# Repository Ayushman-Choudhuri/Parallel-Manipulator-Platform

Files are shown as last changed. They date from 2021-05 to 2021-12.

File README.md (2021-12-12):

# Circle - A Robotic Parallel-Manipulator-Platform

## 1.  Project Description

Circle is an open source 6 DOF robotic parallel manipulator platform. This project was started with the aim of building a stabilization platform for critical payloads like cameras in both linear as well as rotational axes. Additional features will be added as the project matures.   

Project link on my website: https://www.ayushmanchoudhuri.com/circle

## 2. Software

### 2.1 Software Packages Used

#### 2.1.1 Software Development
1. STM32CubeIDE - V1.2.0
2. STM32CubeMX - V6.2.0
3. STM-STUDIO-STM32 - V3.6.0
4. Jupyter Notebook 6.0.1

#### 2.1.2 Hardware Development
1. Solidworks 2018
2. Ultimaker Cura 3.4.1
3. Eagle 9.6.2

### 2.2 Setup

#### 2.2.1 STM Environment

- The Circle_Software.ioc (Software > Circle_Software.ioc) file can be imported into the STM32CubeMX environment and then the pin settings of the STM32F103C8T6 microcontroller can be viewed and modified 
- The .cproject file (Software > .cproject) can be used to import the project into the STM32CUBE IDE Environment.
- Core (Software > Core) contains all the source (Src) and the header files (inc) needed. 
- Variable Viewer (Software>Variable Viewer) contains the .tsc and .tsp files needed to view variables using STM STUDIO

#### 2.2.2 Python - IK Analysis

- The inverse kinematics analysis of the robot can be found in the  "Inverse Kinematics Solver - Python" Folder. The file can be imported into a jupyter notebook and analysed

## 3. Hardware

### 3.1 Controller

The controller is a double sided PCB with the following components mounted on it:
  - DRV8825 Stepper Motor Driver Module
  - STM32F103C8T6 Microcontroller based development board (Blue Pill). The core is an ARM CORTEX M3
  - Mini 360 Step Down Buck Converter Power Module
  - USB to UART TTL 5V 3.3V FT232RL 
  - 3 way DIP switch (To set microstepping mode of the stepper motor drivers)
  - Input port for a MPU 9250 sensor which can be attatched to the end effector for pose feedback
 
 The controller is powered using a 12V 10A SMPS power module

### 3.2 Actuation

The Actuation of the robot links are done using six NEMA 17 4.4 Kgcm motors.

### 3.3 Robot Structure and Links

The robot has a 6 RSS structure. The CAD models can be found in the file - CAD MODELS

### 3.4 Manufacturing

- All the structural support items and end effectors can be 3D printed
- If a 3D printer cannot print the base plates of the robot, they can also be made out of Acrylic sheets (min 5mm) using laser cutting methods
- The S-S links can be made by joining two femals M6 spherical joint bearings using a M6 threaded rod. 

## 4. Future Work
- Closed loop implementation and stablization using MPU 9250 sensor feedback
- Replacement of SMPS with Lithium Polymer Battery
- ROS Implementation 
- Replacing the STM 32 microcontroller with a Raspberry Pi 4

## 5. Contributing

Pull requests are welcome. For major changes, please open an issue first to discuss what you would like to change.

## 6. License

MIT

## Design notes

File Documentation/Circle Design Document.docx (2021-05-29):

CIRCLE – ROBOTIC PARALLEL MANIPULATOR SYSTEM

Written by

Ayushman Choudhuri

Version 2.0

MARCH 2021

DOCUMENT VERSION LOG

Document Version | Date of Release | Document Author | Addition Description
1.0 | 6-01-2021 | Ayushman Choudhuri | Robot Kinematics and Electronic Circuit Diagrams
2.0 | 12-03-2021 | Ayushman Choudhuri | Robot Control System

1. INTRODUCTION
2. NOTATIONS AND SYMBOL DESCRIPTIONS
3. LIST OF FIGURES
4. ROBOT DESCRIPTION

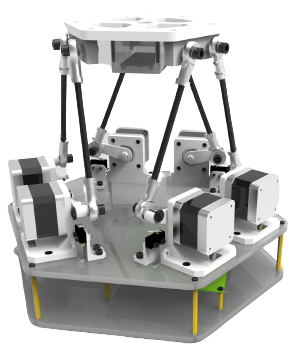
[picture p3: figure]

5. ROBOT INVERSE KINEMATICS

This section describes the inverse kinematics of the robot. Figure 1 depicts the kinematic model of the Circle robotic system. The figure shows the end effector plane, the base plane, and a linkage arm description. The end effector plane is defined by the points {E1, E2, E3, E4, E5, E6}. The base plane is defined by the {B1, B2, B3, B4, B5, B6}. The vector BOE is the translation vector between the base frame and the end-effector frame. The stepper motor arm length is described by ai, and the length of the link with an RSS configuration connecting the stepper motor arm to the end effector is si. The effective link length between the points Ei and Bi is defined by li. The base plane has a origin O at its center with X, Y, and Z as axes. The effector has an origin O’ at its center and X’, Y,’ Z’ as axes.

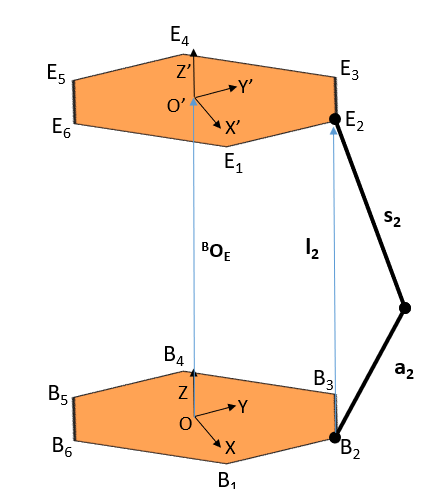
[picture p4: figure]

Figure 1: Kinematic Diagram of the Circle Robot

Each of the points {B1, B2, B3, B4, B5, B6} are the points of intersection of the stepper motor shaft axis and the motor rotation plane. Figure 2 shows the translated frame of reference (X, Y, Z) to a new motor frame of reference (X’’, Y’’, Z’’). Vector bi with its components {Δx, Δy, Δz} is the translation vector between the two frames of reference. Figure 2 shows just one instance of this translation and can be generalized to all the motors.

In the motor frame of reference, the motor plane is the plane on which the motor arm rotates. Angle β is the angle by which the plane is offset in the motor frame of reference, and angle α is the offset angle of the motor arm from the origin position for the respective motor.

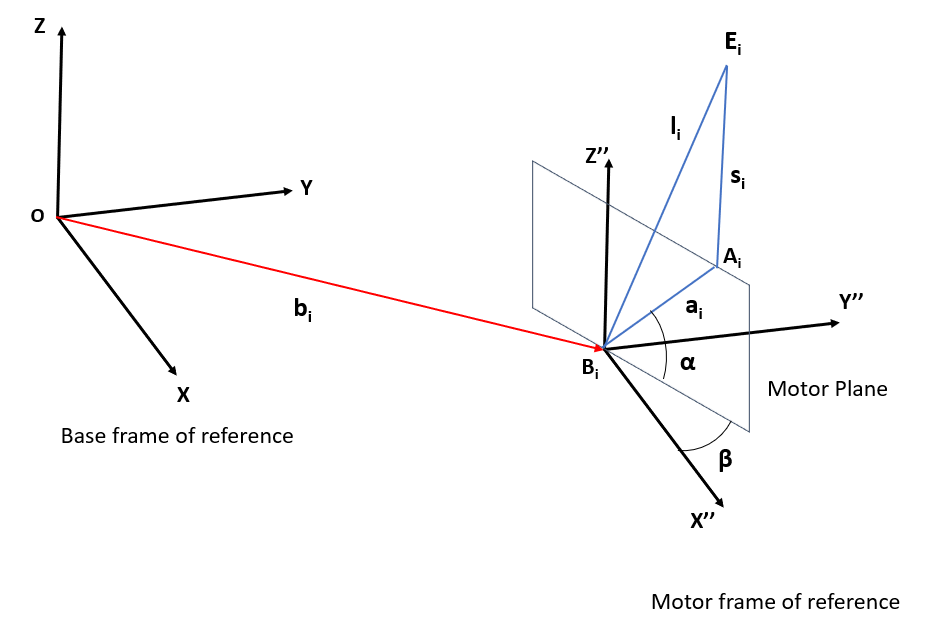
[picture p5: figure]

Figure 2: Description of the motor frame of reference with respect to the base frame origin

The points Ai, Bi and Ei have the following coordinate with respect to the base frame of reference as follows:

Ai = [ Xa, Ya, Za] T

Bi = [ Xb, Yb, Zb] T

Ei = [ Xe, Ye, Ze] T

From Figure 2, we can determine the coordinates for point Ai with respect to the base origin are:

1

Xa = ai.cosα.cosβ + Xb

2

Ya = ai.cosα.sinβ + Yb

3

Za = ai.sinα + Zb

From Pythagoras theorem, we have,

4

ai² = (Xa – Xb)² +(Ya – Yb)² + (Za – Zb)²

5

li² = (Xe – Xb)² +(Ye – Yb)² + (Ze – Zb)²

6

si² = (Xe – Xa)² +(Ye– Ya)² + (Ze – Za)²

substituting equation 4 and 5 in 6, we get

7

li² - (si² – ai²) = 2(Xb² + Yb² + Zb²) + 2Xa(Xe- Xb) + 2Ya(Ye- Yb) + 2Za(Ze – Zb) – 2(XeXb + YeYb +ZeZb)

Now substituting values of Xa, Ya, Za from equation 1,2 and 3, in equation 7 we get

li² - (si² – ai²) = 2aisinα(Ze – Zb) +2aicosα(cosβ(Xe -Xb) + sinβ(Ye - Yb ))

which is an equation of the form

L = Msinα + Ncosα

Using the trigonometric identity for sum of sine waves, we get

asinX + bcosX = csin(X+ɣ)

Where

c = sqrt (a²+b²) and tan ɣ = b/a

We thus have a sine function of α with a phase shift of δ

L = sqrt(M² + N²) sin (α + δ) where δ = tan⁻¹(N/M)

Thus

sin(α + δ) =[ L /(sqrt(M² +N²)]

Thus

αi = sin⁻¹( L/(√(M^2)+ N^2) ) – tan⁻¹( N/M)

8

Where

L = li²- (si²-ai²)

M = 2ai (Ze -Zb)

N = 2ai (cosβ(Xe -Xb) + sinβ(Ye – Yb))

Equation 8 can be used to calculate the required angles of each of the 6 motors using the link geometry parameters and the end effector coordinates as inputs.

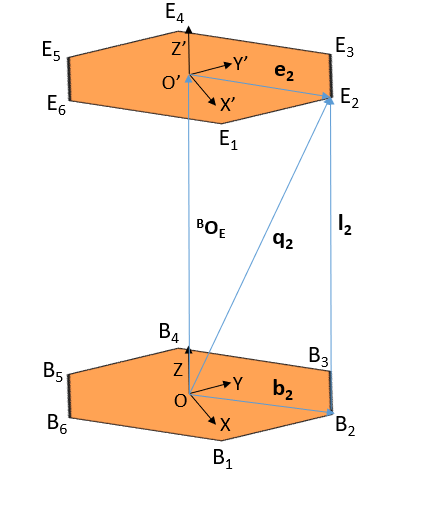
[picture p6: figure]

Figure 3: Position vectors of motor B2 and End Effector point E2 with respect to base frame, motor frame and the end effector frame of reference

From figure 3 , the position vector q2 which describes the point E2 with respect to the base frame of reference.

9

q2 = BOE + BRE.e2

Here BOE is the translation vector between the base frame of reference and the end effector frame of reference. BRE is the

rotation matrix for the end effector frame with respect to the base frame of reference.

The vector q2 can also be written as

10

q2 = b2 + l2

Hence, from equations 9 and 10 we can deduce

l2 = BOE + BRE.e2 - b2

This can be generalised to all the linkages as

11

li = BOE + BRE.ei – bi

The rotation matrix BRE for yaw ψ , pitch θ and Roll φ turns out to be:

BRE = [cosψcosθ, -sinψcosφ+cosψsinθsinφ, sinψsinφ+cosψsinθcosφsinψcosθ, cosψcosφ+sinψsinθsinφ, -cosψsinφ+sinψsinθcosφ-sinθ, cosθsinφ, cosθcosφ]

Equation 11 can be used to calculate the effective link length of any of the linkages when the yaw pitch and roll angles of the end effector frame of reference is known with respect to the base frame of reference.

6. SYSTEM ARCHITECTURE

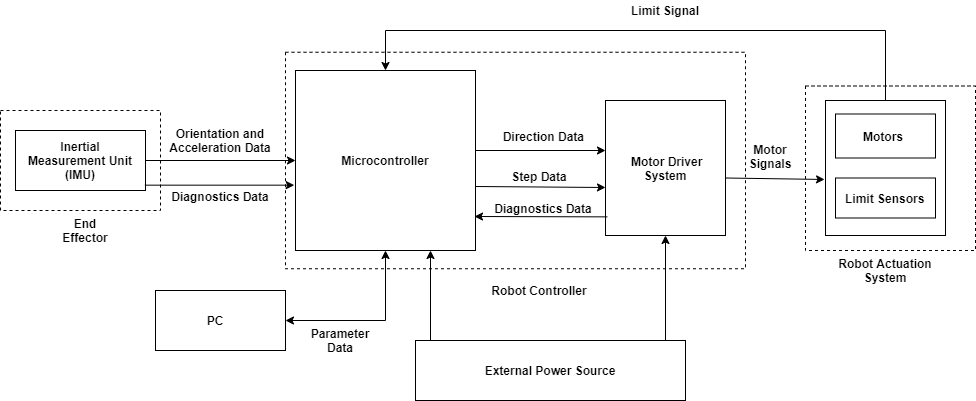
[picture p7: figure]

Figure 4: Circle System Architecture

  6.1. MICROCONTROLLER
  6.2. MOTOR DRIVER SYSTEM
  6.3. ROBOT ACTUATION SYSTEM
  6.4. INERTIAL MEASUREMENT UNIT
7. MECHANICAL DESIGN
  7.1. GENERAL DESCRIPTION
  7.2. ROBOT BASE
  7.3. ELECTRONICS BAY
  7.4. ROBOT LINKS
  7.5. END EFFECTOR DESIGN
  7.6. MANUFACTURING DETAILS
8. CONTROL SYSTEM DESIGN
9. SOFTWARE ARCHITECTURE
10. ELECTRONIC SCHEMATIC (V1)

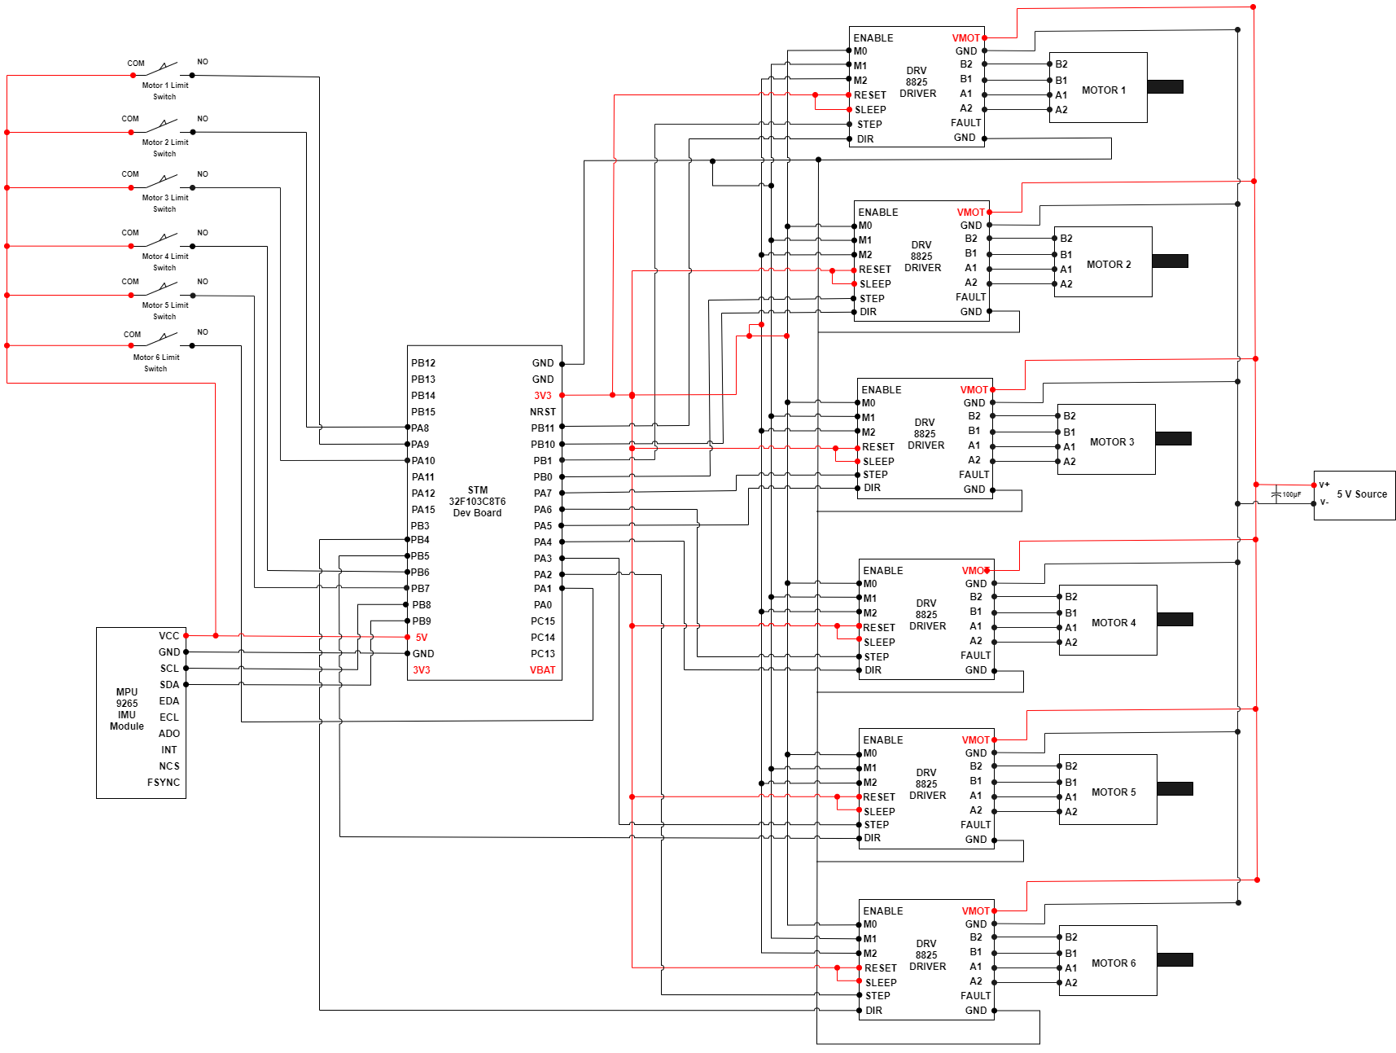
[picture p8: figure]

Figure 5: Electronic Circuit Diagram V1

11. ROBOT PARAMETERS
  11.1. END EFFECTOR PARAMETERS

Coordinates (in mm) of the end effector pivot point coordinates with respect to the end effector frame of reference.

E = [-73.7, +19.46, 0-53.7, +54.1, 0+53.7, +54.1, 0+73.7, +19.46, 0+20, -73.55, 0-20, -73.55, 0]

  11.2. BASE PARAMETERS

Coordinates (in mm) of the base pivot point coordinates with respect to the base frame of reference.

B = [-81.63, +0.36, 0-41.13, +70.51, 0+41.13, +70.51, 0+81.63, +0.36, 0+40.5, -70.87, 0-81.63, -70.87, 0]

  11.3. HOME POSITION OFFSET PARAMETERS
  11.4. INERTIAL MEASUREMENT UNIT PARAMETERS (MPU 9250)
  11.5. STEPPER MOTOR DRIVER PARAMETERS (DRV8825)
12. REFERENCES

[1] https://invensense.tdk.com/wp-content/uploads/2015/02/PS-MPU-9250A-01-v1.1.pdf

[2] https://cdn.sparkfun.com/assets/learn_tutorials/5/5/0/MPU-9250-Register-Map.pdf

[3]https://github.com/kriswiner/MPU9250/tree/master/Documents

[4]https://github.com/kriswiner/MPU9250/tree/master/STM32F401

[5]https://github.com/kriswiner/MPU9250

[6]https://www.ti.com/lit/ds/symlink/drv8825.pdf?ts=1615789139713&ref_url=https%253A%252F%252Fwww.google.com%252F

[7] https://www.pololu.com/product/2133

[8] https://www.youtube.com/watch?v=6IAkYpmA1DQ&ab_channel=HowToMechatronics

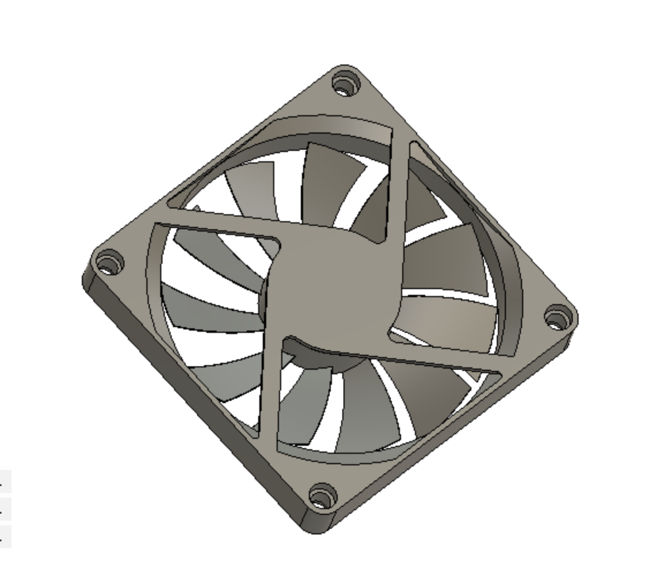
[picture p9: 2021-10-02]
CAD Models/Electronics/80 mm Fan/Screen Shot 2019-12-02 at 6.14.03 PM.png

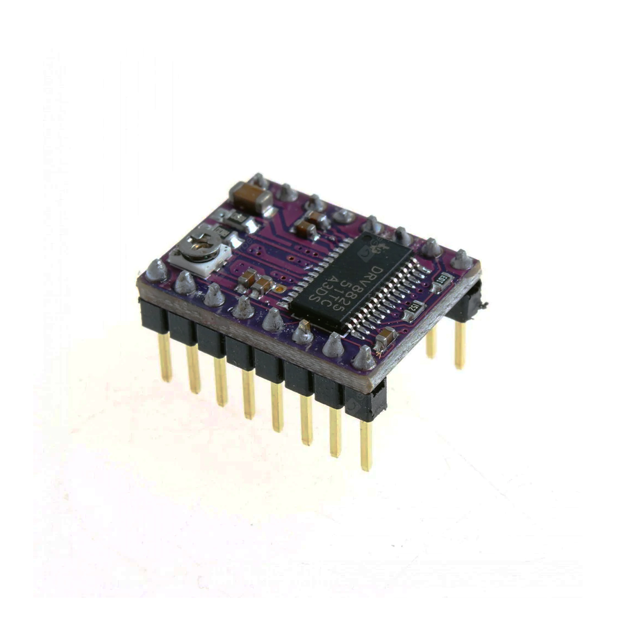
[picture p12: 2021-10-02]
CAD Models/Electronics/DRV8825/Driver DRV8825.jpg

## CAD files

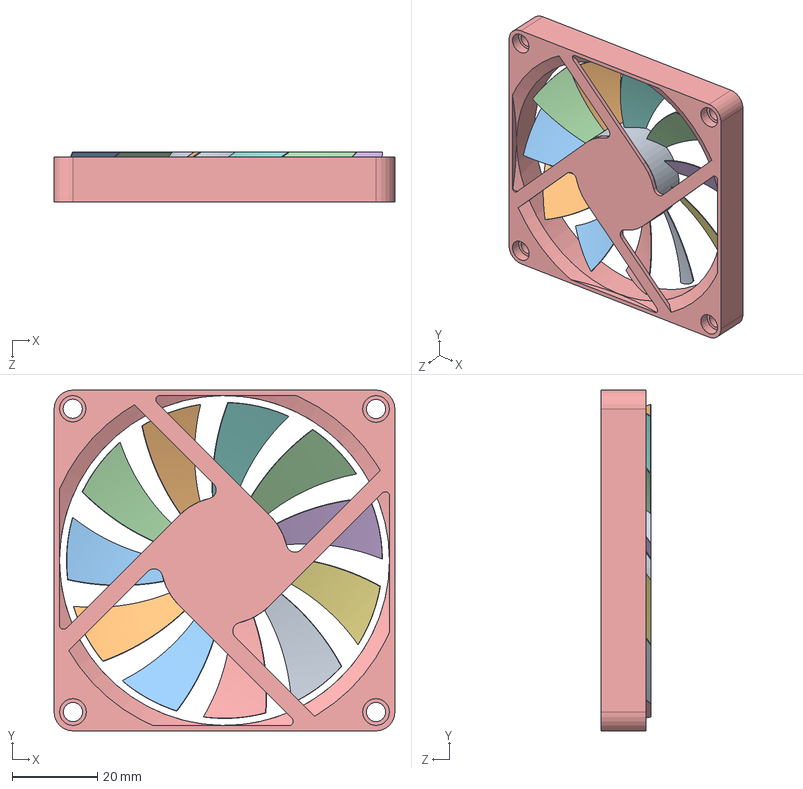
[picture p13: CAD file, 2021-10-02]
CAD Models/Electronics/80 mm Fan/GDSTIME - 5v Fan_13.sldasm
80.0 x 80.0 x 11.8 mm
GDSTIME - 5v Fan_6
GDSTIME - 5v Fan_8
GDSTIME - 5v Fan_4
GDSTIME - 5v Fan_3
GDSTIME - 5v Fan_12
GDSTIME - 5v Fan_5
GDSTIME - 5v Fan_10
GDSTIME - 5v Fan_7
GDSTIME - 5v Fan_11
GDSTIME - 5v Fan_9
GDSTIME - 5v Fan_2
GDSTIME - 5v Fan
GDSTIME - 5v Fan_1

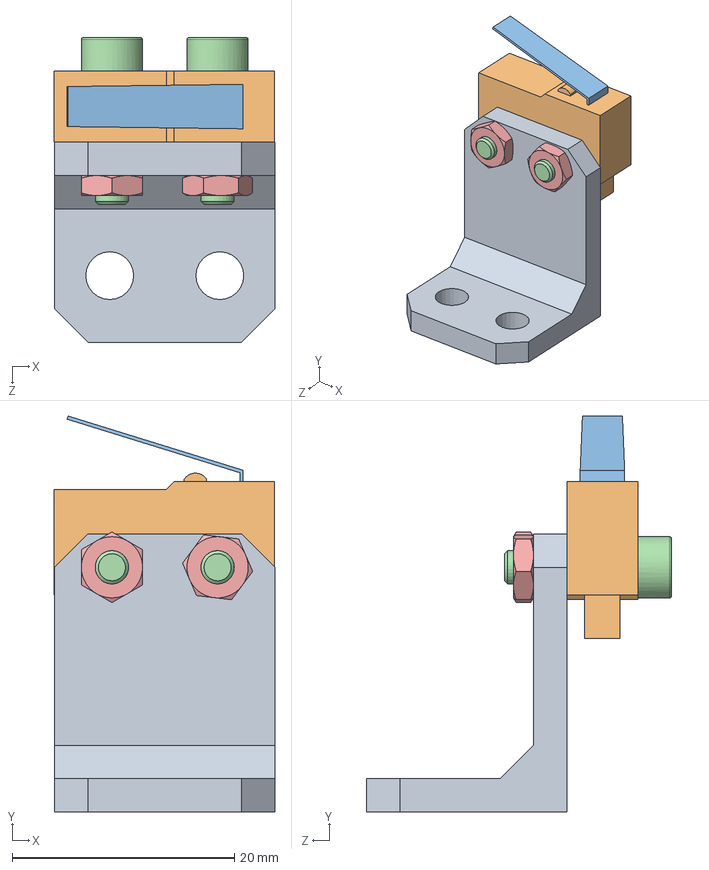
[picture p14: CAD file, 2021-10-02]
CAD Models/Electronics/Limit Switch/limit switch module assembly.SLDASM
19.9 x 35.6 x 27.4 mm
Limit Switch mount
SS_01GL_E_BASE
SS_01GL_E_ACTUATOR
socket head cap screw_iso x 2
hex thin nut chamfered gradeab_iso x 2

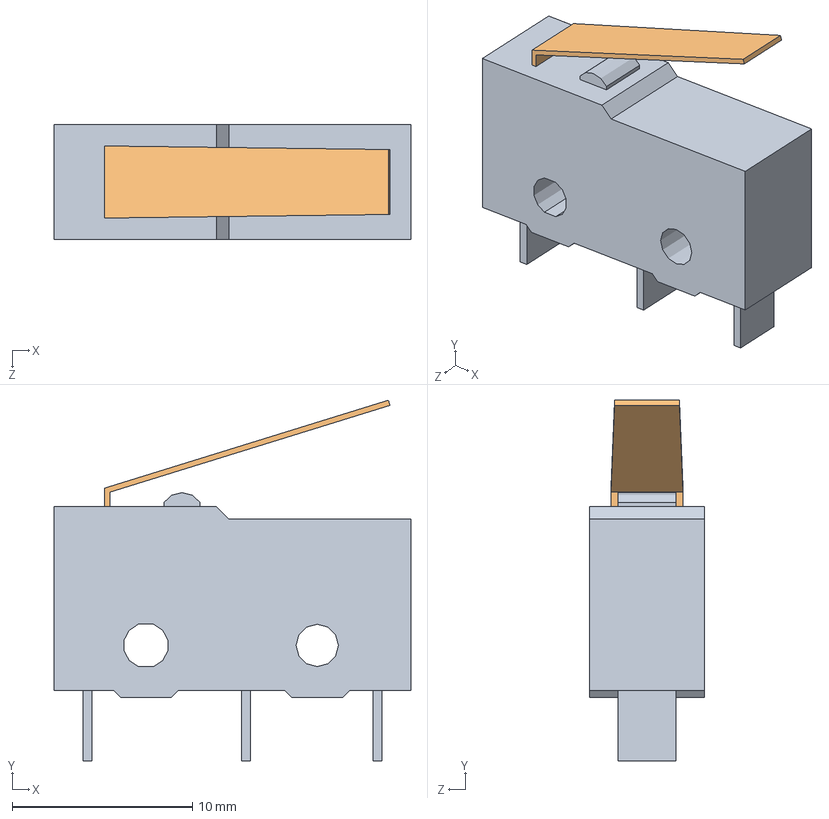
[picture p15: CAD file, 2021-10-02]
CAD Models/Electronics/Limit Switch/OMRON_SS_5GL/OMRON_ss-5gl.SLDASM
19.8 x 20.0 x 6.40 mm
SS_01GL_E_BASE
SS_01GL_E_ACTUATOR

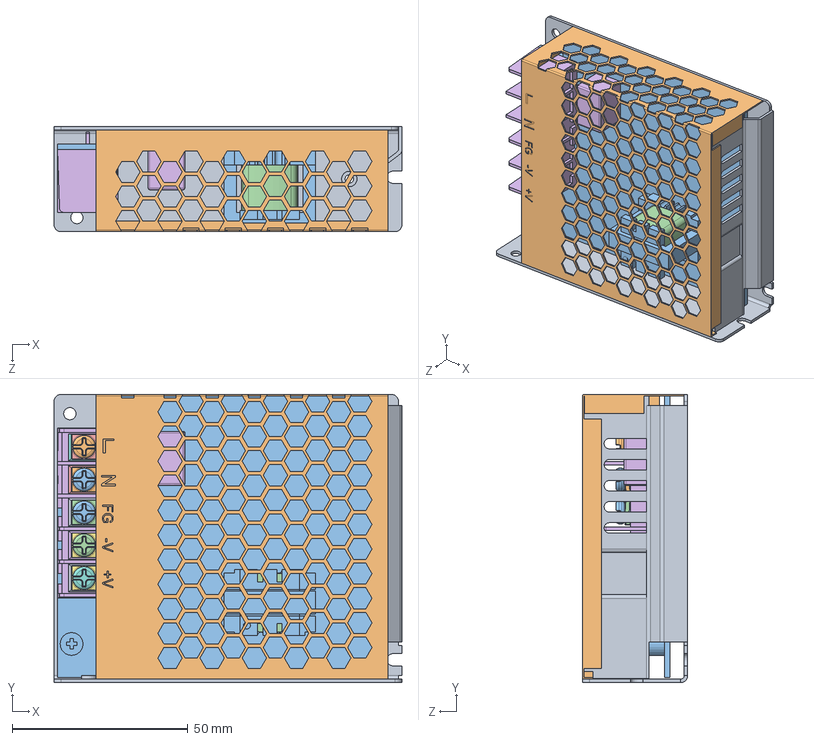
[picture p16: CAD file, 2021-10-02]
CAD Models/Electronics/SMPS/SMPS/kimj388CFB76w7zk_47.sldasm
99.0 x 82.0 x 30.0 mm
kimj388CFB76w7zk_11
kimj388CFB76w7zk_27
kimj388CFB76w7zk_16
kimj388CFB76w7zk_30
kimj388CFB76w7zk_18
kimj388CFB76w7zk_45
kimj388CFB76w7zk_35
kimj388CFB76w7zk_26
kimj388CFB76w7zk_15
kimj388CFB76w7zk_32
kimj388CFB76w7zk_13
kimj388CFB76w7zk
kimj388CFB76w7zk_34
kimj388CFB76w7zk_17
kimj388CFB76w7zk_4
kimj388CFB76w7zk_42
kimj388CFB76w7zk_37
kimj388CFB76w7zk_28
kimj388CFB76w7zk_19
kimj388CFB76w7zk_38
kimj388CFB76w7zk_8
kimj388CFB76w7zk_29
kimj388CFB76w7zk_2
kimj388CFB76w7zk_22
kimj388CFB76w7zk_20
kimj388CFB76w7zk_5
kimj388CFB76w7zk_21
kimj388CFB76w7zk_44
kimj388CFB76w7zk_40
kimj388CFB76w7zk_10

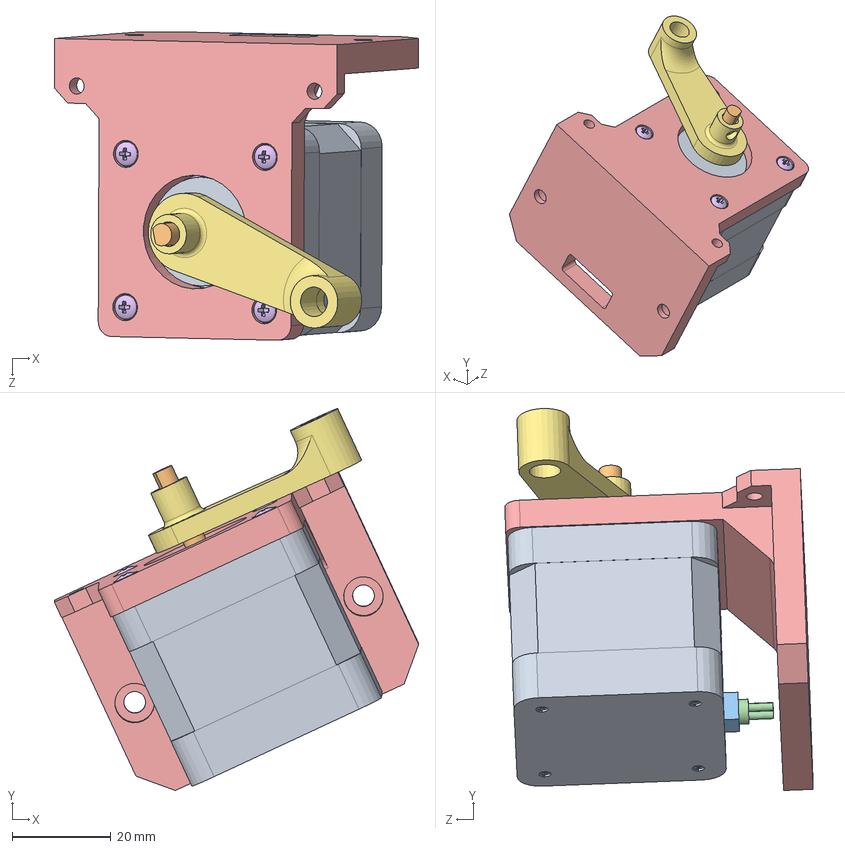
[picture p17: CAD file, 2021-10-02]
CAD Models/Robot Base/Robot Base Skeleton/Actuation Module Assembly.SLDASM
73.6 x 77.2 x 62.3 mm
NEMA17
Shaft
cables_cover
cables
Stepper Motor Mount
pan head cross recess screw_iso x 4
Motor Coupler

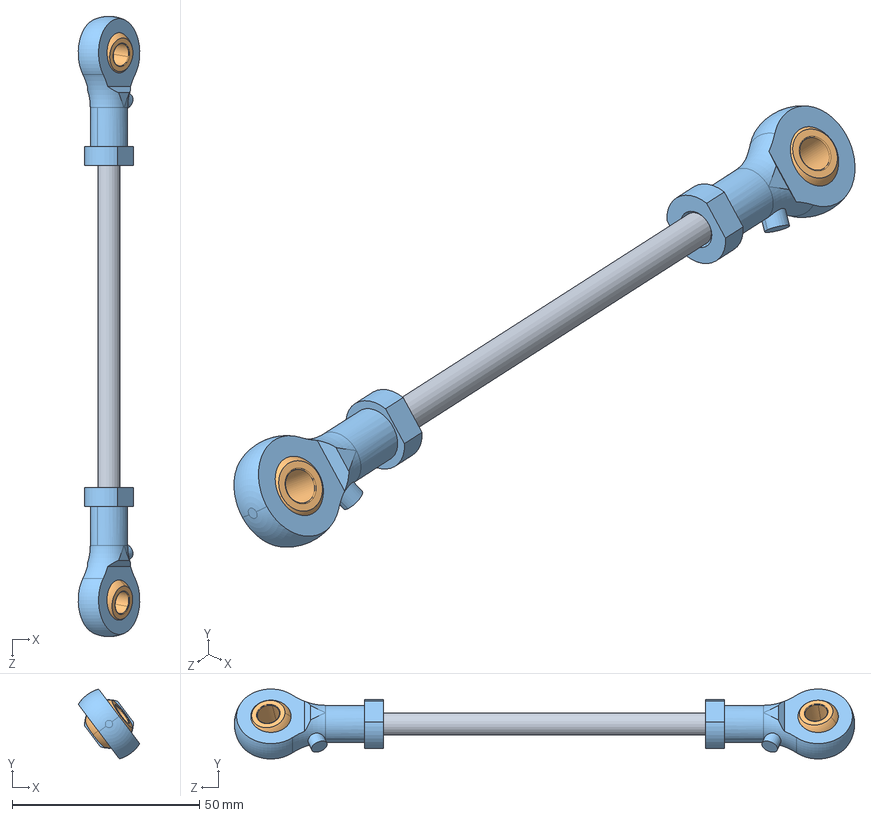
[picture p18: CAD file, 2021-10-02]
CAD Models/Robot Links/Link 2 (Spherical Joint Rod)/Link 2 assembly.SLDASM
16.4 x 18.6 x 165.4 mm
M6 Threaded Rod
PHSA6_3 x 2
PHSA6_5 x 2

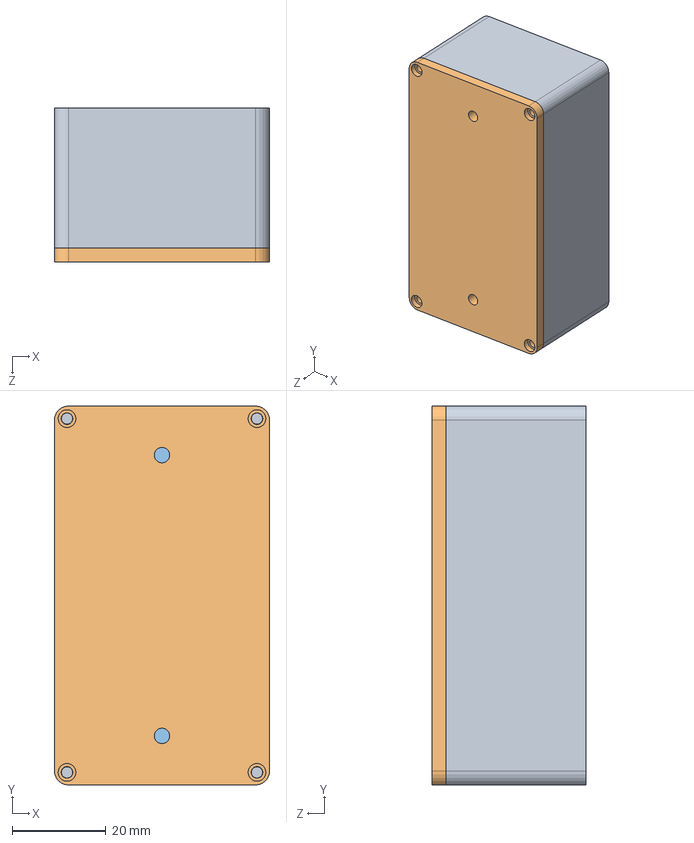
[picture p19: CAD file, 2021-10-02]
CAD Models/Robot Sensors/IMU Module 2/IMU Module 2 Assembly.SLDASM
46.0 x 81.0 x 33.0 mm
IMU module enclosure base
IMU Module Enclosure Top
base board

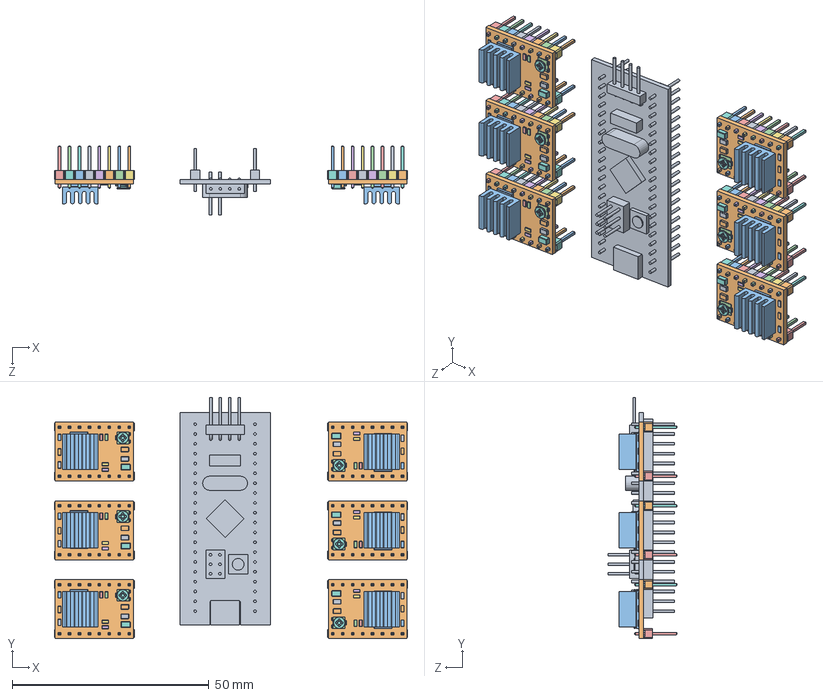
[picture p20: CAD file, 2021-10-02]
CAD Models/Electronics/Onboard controller assembly/full onboard controller assembly.SLDASM
89.7 x 61.3 x 17.6 mm
stm32f103c8t6-board
Driver DRV8825_23 x 6
Driver DRV8825_15 x 6
Driver DRV8825_3 x 6
Driver DRV8825_18 x 6
Driver DRV8825_22 x 6
Driver DRV8825_38 x 6
Driver DRV8825_44 x 6
Driver DRV8825_32 x 6
Driver DRV8825_36 x 6
Driver DRV8825_14 x 6
Driver DRV8825_27 x 6
Driver DRV8825 x 6
Driver DRV8825_2 x 6
Driver DRV8825_40 x 6
Driver DRV8825_35 x 6
Driver DRV8825_48 x 6
Driver DRV8825_34 x 6
Driver DRV8825_43 x 6
Driver DRV8825_25 x 6
Driver DRV8825_5 x 6
Driver DRV8825_31 x 6
Driver DRV8825_10 x 6
Driver DRV8825_28 x 6
Driver DRV8825_33 x 6
Driver DRV8825_26 x 6
Driver DRV8825_1 x 6
Driver DRV8825_39 x 6
Driver DRV8825_8 x 6
Driver DRV8825_6 x 6
Driver DRV8825_47 x 6
Driver DRV8825_19 x 6
Driver DRV8825_13 x 6
Driver DRV8825_16 x 6
Driver DRV8825_12 x 6
Driver DRV8825_9 x 6
Driver DRV8825_41 x 6
Driver DRV8825_24 x 6
Driver DRV8825_4 x 6
Driver DRV8825_46 x 6
Driver DRV8825_29 x 6
Driver DRV8825_49 x 6
Driver DRV8825_45 x 6
Driver DRV8825_42 x 6
Driver DRV8825_30 x 6
Driver DRV8825_20 x 6
Driver DRV8825_7 x 6
Driver DRV8825_17 x 6
Driver DRV8825_11 x 6
Driver DRV8825_37 x 6
Driver DRV8825_21 x 6

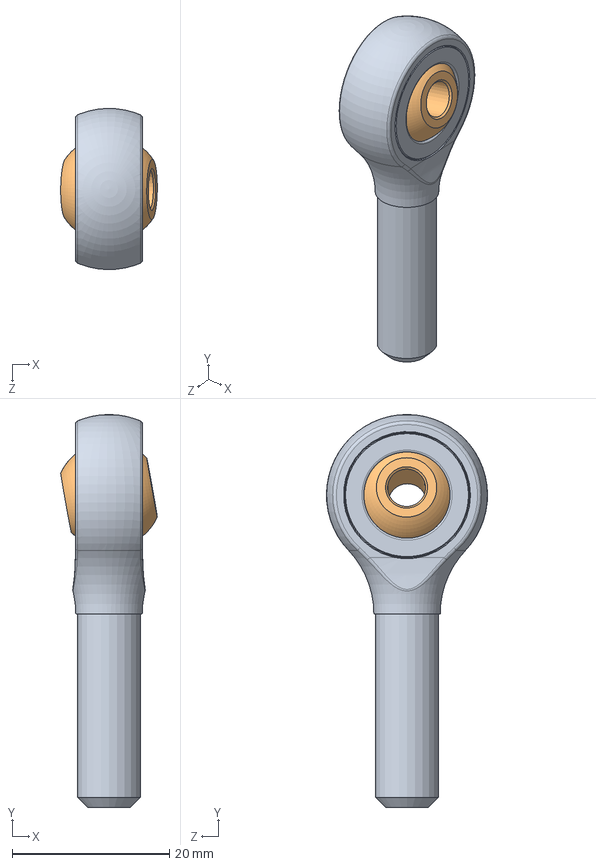
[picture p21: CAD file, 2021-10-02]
CAD Models/Robot Links/Link 2 (Spherical Joint Rod)/Spherical Joint/Ball Joints Male/ASx-xxT Male Rod End Imperial.SLDASM
12.3 x 49.9 x 20.5 mm
ASx-xxT Male Rod End Imperial Body
ASx-xxT Male Rod End Imperial Ball

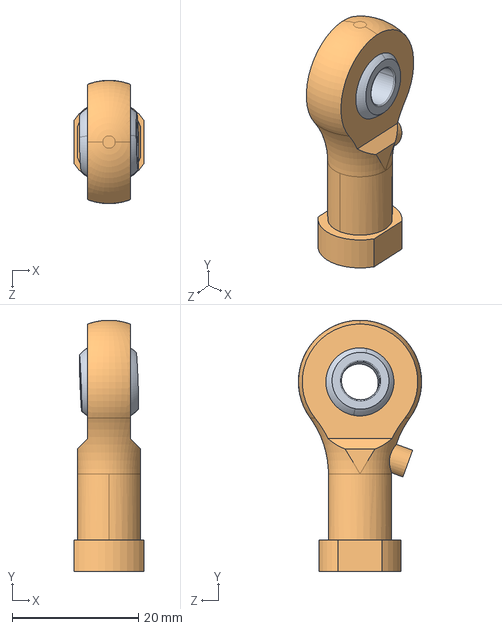
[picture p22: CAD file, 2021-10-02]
CAD Models/Robot Links/Link 2 (Spherical Joint Rod)/Spherical Joint/M6 Ball Joint/SOLIDWORKS/Rod End Bearing Assembly.SLDASM
11.0 x 39.7 x 19.5 mm
PHSA6_3
PHSA6_5

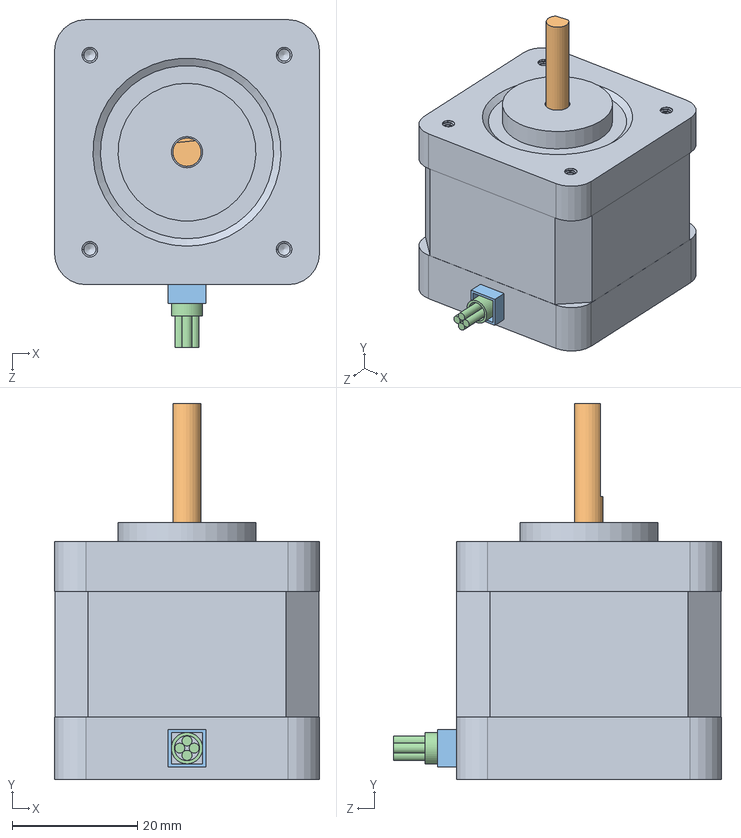
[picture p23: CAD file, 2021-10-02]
CAD Models/Robot Base/Stepper Motors/NEMA17_2PhaseSingle.SLDASM
42.3 x 60.0 x 52.3 mm
NEMA17
Shaft
cables_cover
cables

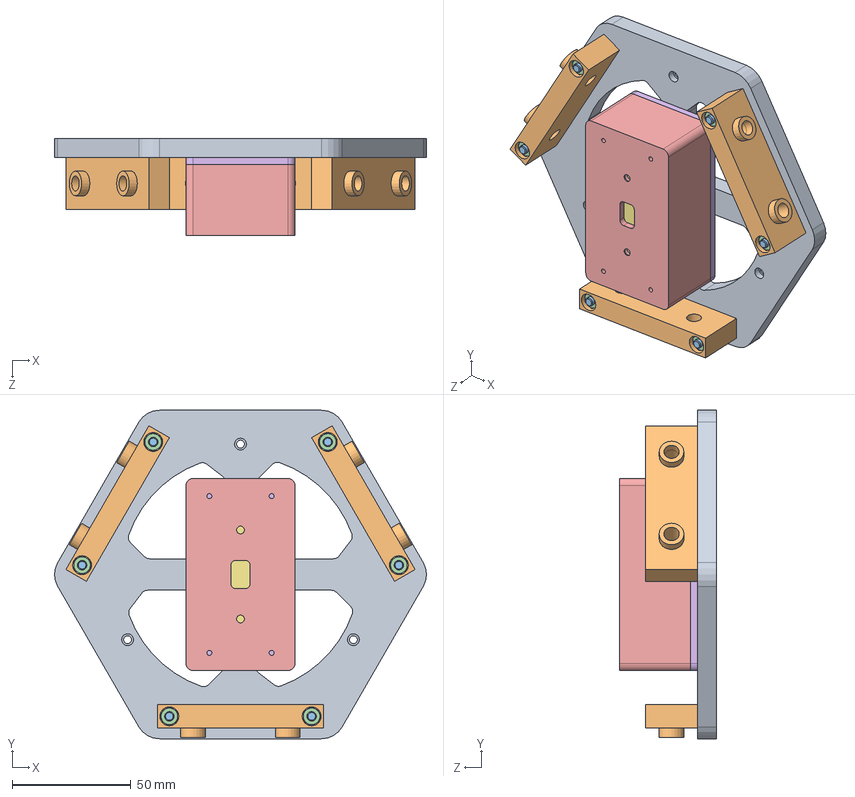
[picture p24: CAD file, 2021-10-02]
CAD Models/Robot End Effector/CIRCLE end effector/CIRCLE End effector assembly.SLDASM
156.9 x 138.6 x 41.0 mm
End Effector Base
End Effector Joint Blocks x 3
socket head cap screw_iso x 6
hex thin nut chamfered gradeab_iso x 6
IMU module enclosure base
IMU Module Enclosure Top
base board
pan head cross recess screw_iso x 4
slotted pan head screw_iso x 2

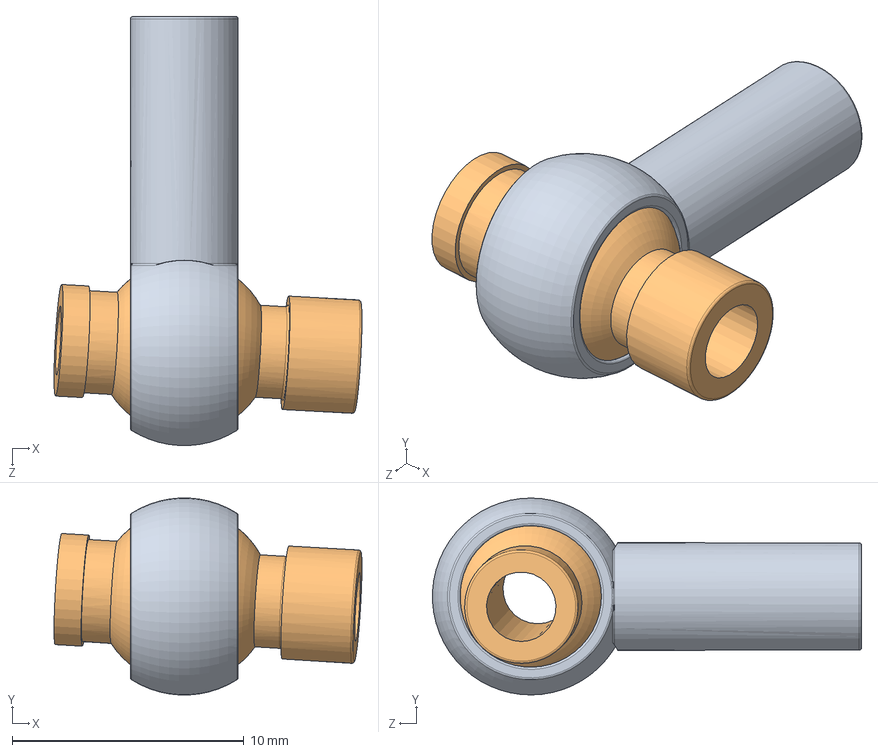
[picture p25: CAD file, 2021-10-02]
CAD Models/Robot Links/Link 2 (Spherical Joint Rod)/Spherical Joint/Ball joint assembly new.SLDASM
13.3 x 8.49 x 18.5 mm
ENclosure
ball

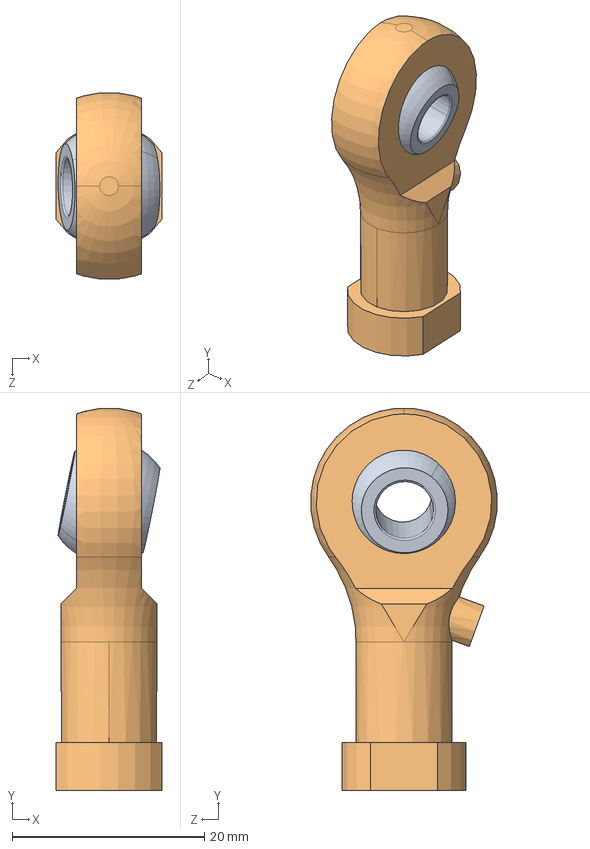
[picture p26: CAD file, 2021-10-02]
CAD Models/Robot Links/Link 2 (Spherical Joint Rod)/Spherical Joint/M6 Ball Joint/SOLIDWORKS/PHSA6.sldasm
11.0 x 39.7 x 19.4 mm
PHSA6_3
PHSA6_5

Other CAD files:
CAD Models/Robot Base/Electronics CAD/Parts/Limit Switch/Omron SS 5GL/OMRON_SS_5GL/OMRON SS 5GL Limit Switch.SLDASM
CAD Models/Robot Base/Electronics CAD/Parts/Limit Switch/Omron SS 5GL/OMRON_SS_5GL/OMRON_ss-5gl.SLDASM
CAD Models/Robot Links/Link 2 (Spherical Joint Rod)/Spherical Joint/Ball Joints Female/ASx-xxT Female Rod End Imperial.SLDASM
CAD Models/Electronics/80 mm Fan/80mm fan.SLDASM
CAD Models/Electronics/100x100 new PCB model.SLDPRT
CAD Models/Electronics/40 mm fan/40x40x10 DC Fan.SLDPRT
CAD Models/Electronics/40 mm fan/40x40x10 DC Fan.STEP
CAD Models/Electronics/80 mm Fan/GDSTIME - 5v Fan.f3d
CAD Models/Electronics/80 mm Fan/GDSTIME - 5v Fan.iges
CAD Models/Electronics/80 mm Fan/GDSTIME - 5v Fan.sldprt
CAD Models/Electronics/80 mm Fan/GDSTIME - 5v Fan.step
CAD Models/Electronics/80 mm Fan/GDSTIME - 5v Fan_1.sldprt
CAD Models/Electronics/80 mm Fan/GDSTIME - 5v Fan_10.sldprt
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

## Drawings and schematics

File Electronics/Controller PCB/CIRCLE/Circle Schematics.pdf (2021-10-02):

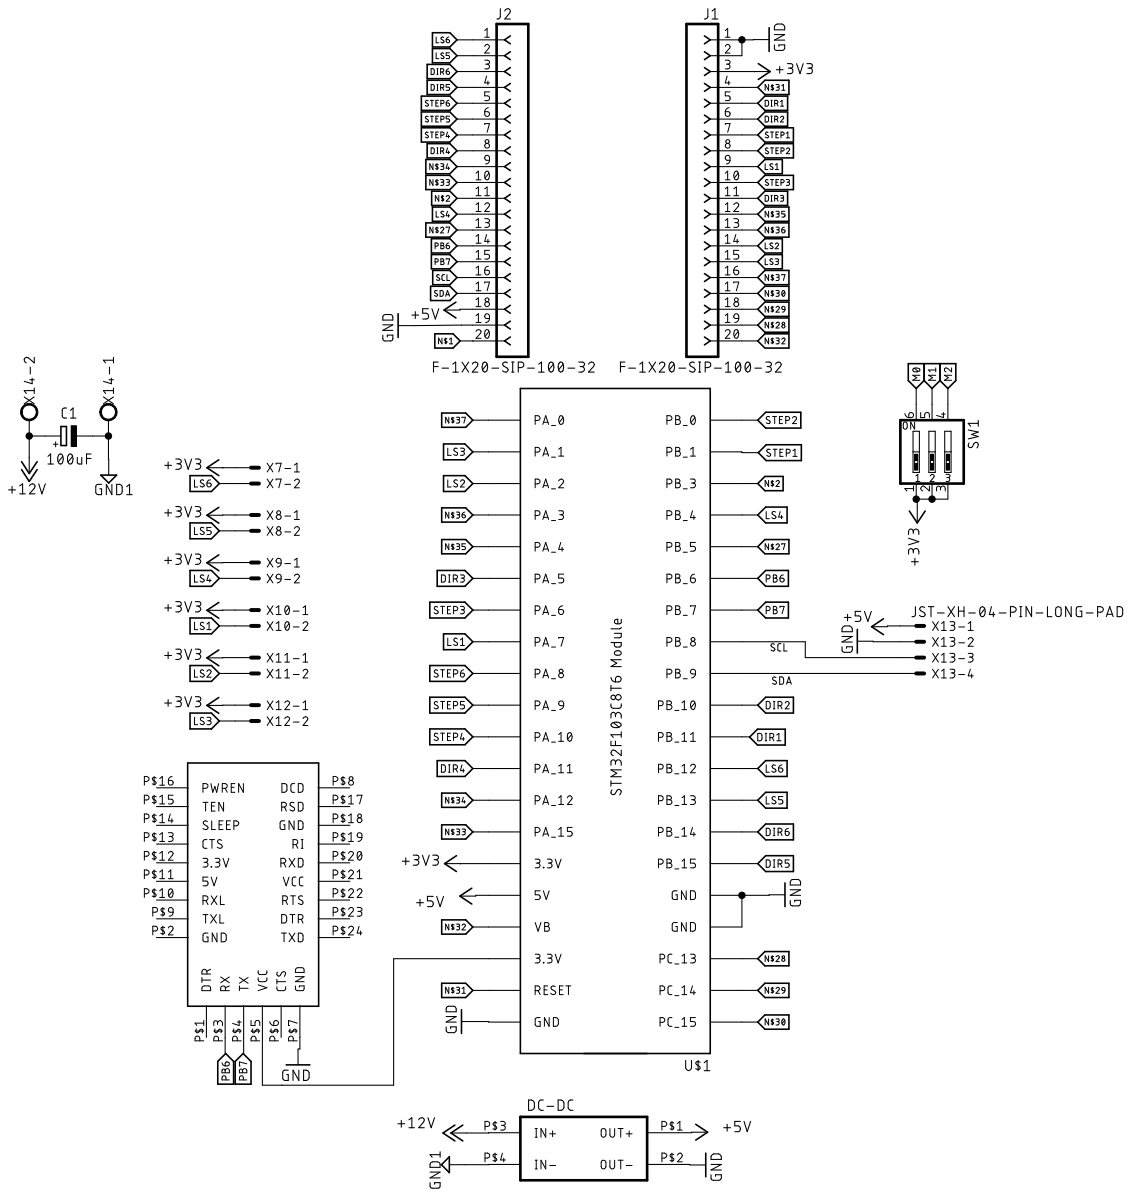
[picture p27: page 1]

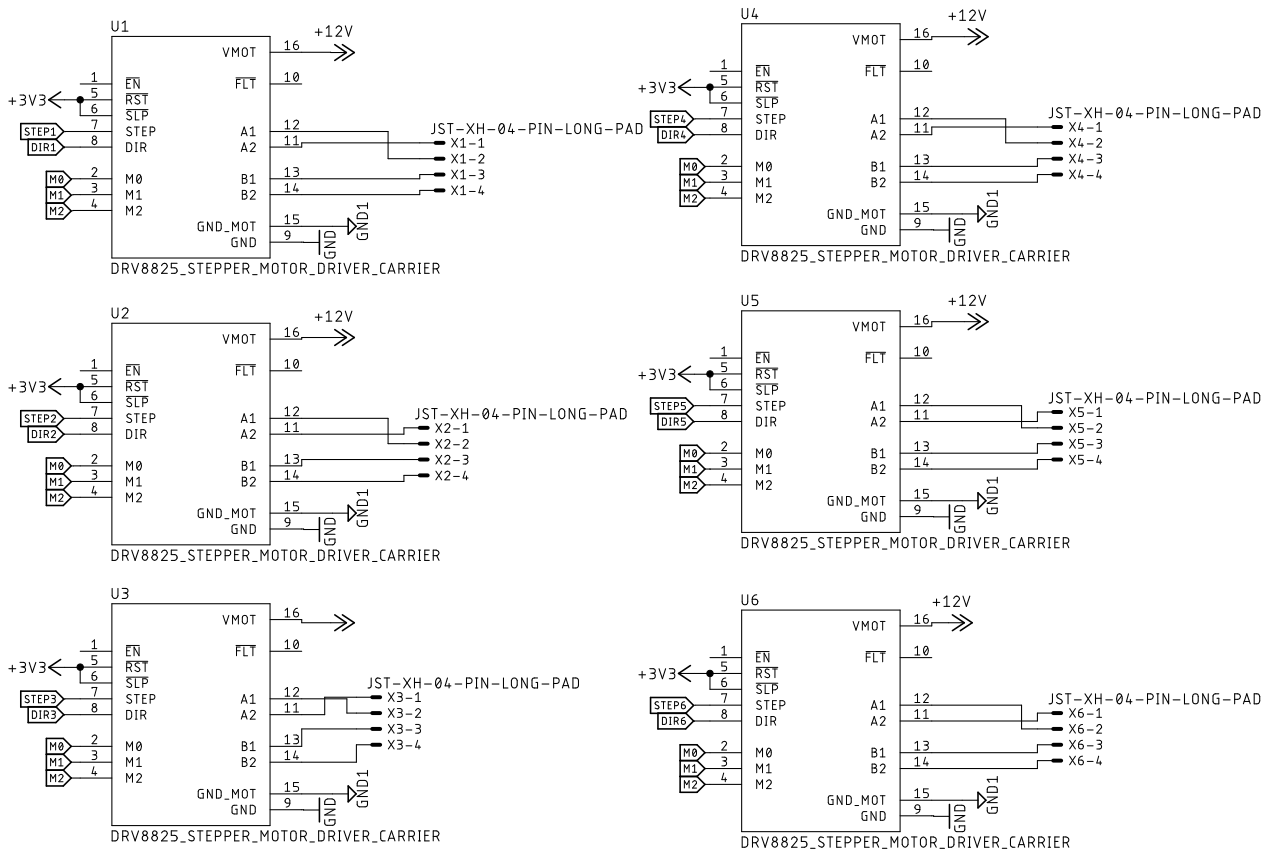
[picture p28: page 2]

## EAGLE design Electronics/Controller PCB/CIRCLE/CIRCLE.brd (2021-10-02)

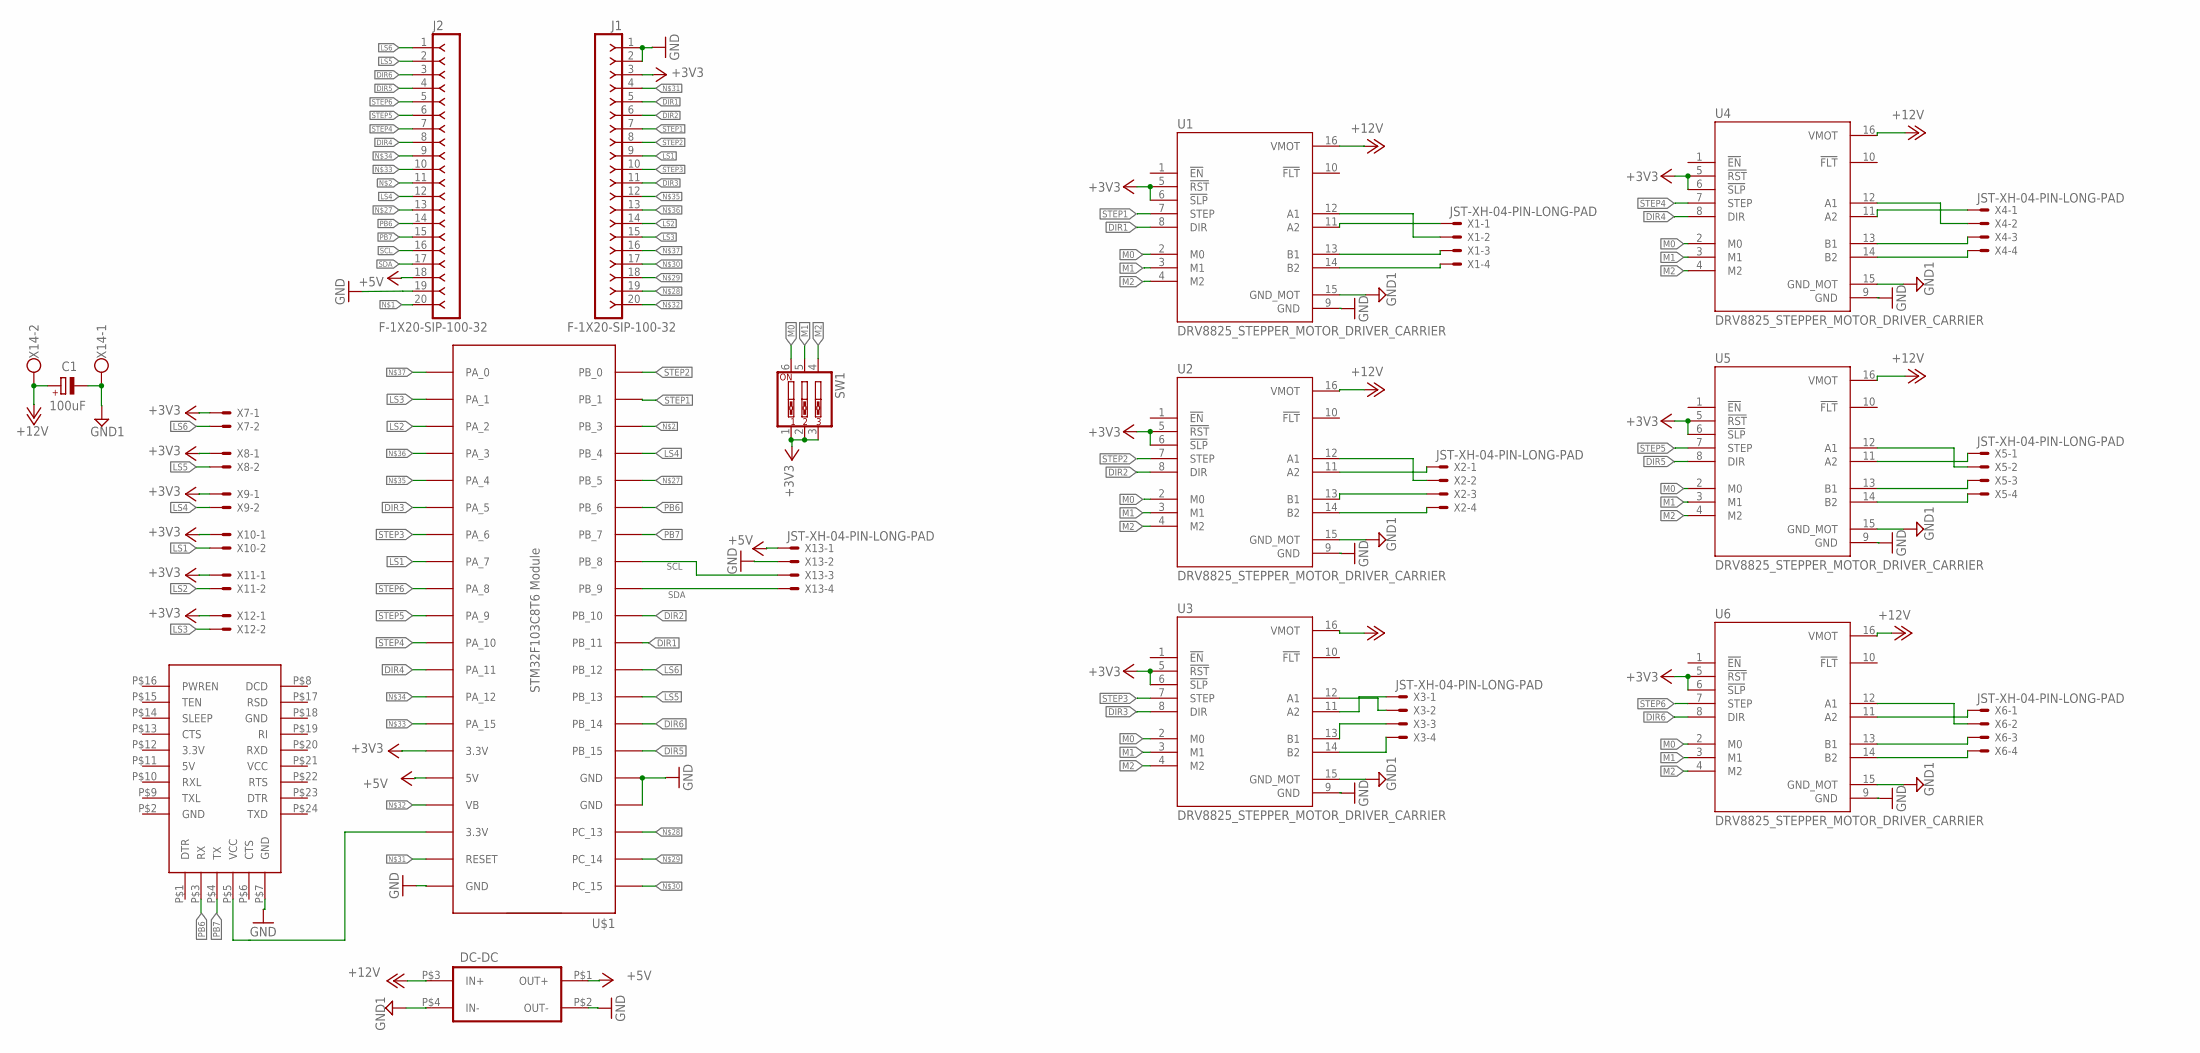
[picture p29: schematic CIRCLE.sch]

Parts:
C1: 100uF; E3,5-8
J1, J2: F-1X20-SIP-100-32; SIP-100-20-32
SW1: SW_DIP-3; EDG-03
U1, U2, U3, U4, U5, U6: DRV8825_STEPPER_MOTOR_DRIVER_CARRIER; IC_DRV8825_STEPPER_MOTOR_DRIVER_CARRIER
U$1: STM32F103C8T6-MODULE
U$2: DC-DC_CONV
U$3: FT232RL_FTDI
X1, X2, X3, X4, X5, X6, X13: JST-XH-04-PIN-LONG-PAD; JST-XH-04-PACKAGE-LONG-PAD
X7, X8, X9, X10, X11, X12: JST-XH-02-PIN-LONG-PAD; JST-XH-02-PACKAGE-LONG-PAD
X14: W237-102

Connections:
+3V3: J1.3, SW1.1, SW1.2, SW1.3, U1.5 (!RST), U1.6 (!SLP), U2.5 (!RST), U2.6 (!SLP), U3.5 (!RST), U3.6 (!SLP), U4.5 (!RST), U4.6 (!SLP), U5.5 (!RST), U5.6 (!SLP), U6.5 (!RST), U6.6 (!SLP), U$1.3.3V@2 (3.3V), X7.1, X8.1, X9.1, X10.1, X11.1, X12.1
+5V: J2.18, U$1.5V, U$2.P$1 (OUT+), X13.1
+12V: C1.+, U1.16 (VMOT), U2.16 (VMOT), U3.16 (VMOT), U4.16 (VMOT), U5.16 (VMOT), U6.16 (VMOT), U$2.P$3 (IN+), X14.2
DIR1: J1.5, U1.8 (DIR), U$1.PB_11
DIR2: J1.6, U2.8 (DIR), U$1.PB_10
DIR3: J1.11, U3.8 (DIR), U$1.PA_5
DIR4: J2.8, U4.8 (DIR), U$1.PA_11
DIR5: J2.4, U5.8 (DIR), U$1.PB_15
DIR6: J2.3, U6.8 (DIR), U$1.PB_14
GND: J1.1, J1.2, J2.19, U1.9 (GND), U2.9 (GND), U3.9 (GND), U4.9 (GND), U5.9 (GND), U6.9 (GND), U$1.GND@1 (GND), U$1.GND@2 (GND), U$1.GND@3 (GND), U$2.P$2 (OUT-), U$3.P$7 (GND), X13.2
GND1: C1.-, U1.15 (GND_MOT), U2.15 (GND_MOT), U3.15 (GND_MOT), U4.15 (GND_MOT), U5.15 (GND_MOT), U6.15 (GND_MOT), U$2.P$4 (IN-), X14.1
LS1: J1.9, U$1.PA_7, X10.2
LS2: J1.14, U$1.PA_2, X11.2
LS3: J1.15, U$1.PA_1, X12.2
LS4: J2.12, U$1.PB_4, X9.2
LS5: J2.2, U$1.PB_13, X8.2
LS6: J2.1, U$1.PB_12, X7.2
M0: SW1.6, U1.2 (M0), U2.2 (M0), U3.2 (M0), U4.2 (M0), U5.2 (M0), U6.2 (M0)
M1: SW1.5, U1.3 (M1), U2.3 (M1), U3.3 (M1), U4.3 (M1), U5.3 (M1), U6.3 (M1)
M2: SW1.4, U1.4 (M2), U2.4 (M2), U3.4 (M2), U4.4 (M2), U5.4 (M2), U6.4 (M2)
unnamed: J2.20, U$1.3.3V@1 (3.3V), U$3.P$5 (VCC)
unnamed: J2.11, U$1.PB_3
unnamed: U1.14 (B2), X1.4
unnamed: U1.13 (B1), X1.3
unnamed: U1.12 (A1), X1.2
unnamed: U1.11 (A2), X1.1
unnamed: U2.14 (B2), X2.4
unnamed: U2.13 (B1), X2.3
unnamed: U2.11 (A2), X2.1
unnamed: U2.12 (A1), X2.2
unnamed: U4.14 (B2), X4.4
unnamed: U4.13 (B1), X4.3
unnamed: U4.11 (A2), X4.1
unnamed: U4.12 (A1), X4.2
unnamed: U5.14 (B2), X5.4
unnamed: U5.13 (B1), X5.3
unnamed: U5.11 (A2), X5.1
unnamed: U5.12 (A1), X5.2
unnamed: U6.14 (B2), X6.4
unnamed: U6.13 (B1), X6.3
unnamed: U6.11 (A2), X6.1
unnamed: U6.12 (A1), X6.2
unnamed: U3.14 (B2), X3.4
unnamed: U3.13 (B1), X3.3
unnamed: U3.11 (A2), X3.1
unnamed: U3.12 (A1), X3.2
unnamed: J2.13, U$1.PB_5
unnamed: J1.19, U$1.PC_13
unnamed: J1.18, U$1.PC_14
unnamed: J1.17, U$1.PC_15
unnamed: J1.4, U$1.RESET
unnamed: J1.20, U$1.VB
unnamed: J2.10, U$1.PA_15
unnamed: J2.9, U$1.PA_12
unnamed: J1.12, U$1.PA_4
unnamed: J1.13, U$1.PA_3
unnamed: J1.16, U$1.PA_0
PB6: J2.14, U$1.PB_6, U$3.P$3 (RX)
PB7: J2.15, U$1.PB_7, U$3.P$4 (TX)
SCL: J2.16, U$1.PB_8, X13.3
SDA: J2.17, U$1.PB_9, X13.4
STEP1: J1.7, U1.7 (STEP), U$1.PB_1
STEP2: J1.8, U2.7 (STEP), U$1.PB_0
STEP3: J1.10, U3.7 (STEP), U$1.PA_6
STEP4: J2.7, U4.7 (STEP), U$1.PA_10
STEP5: J2.6, U5.7 (STEP), U$1.PA_9
STEP6: J2.5, U6.7 (STEP), U$1.PA_8

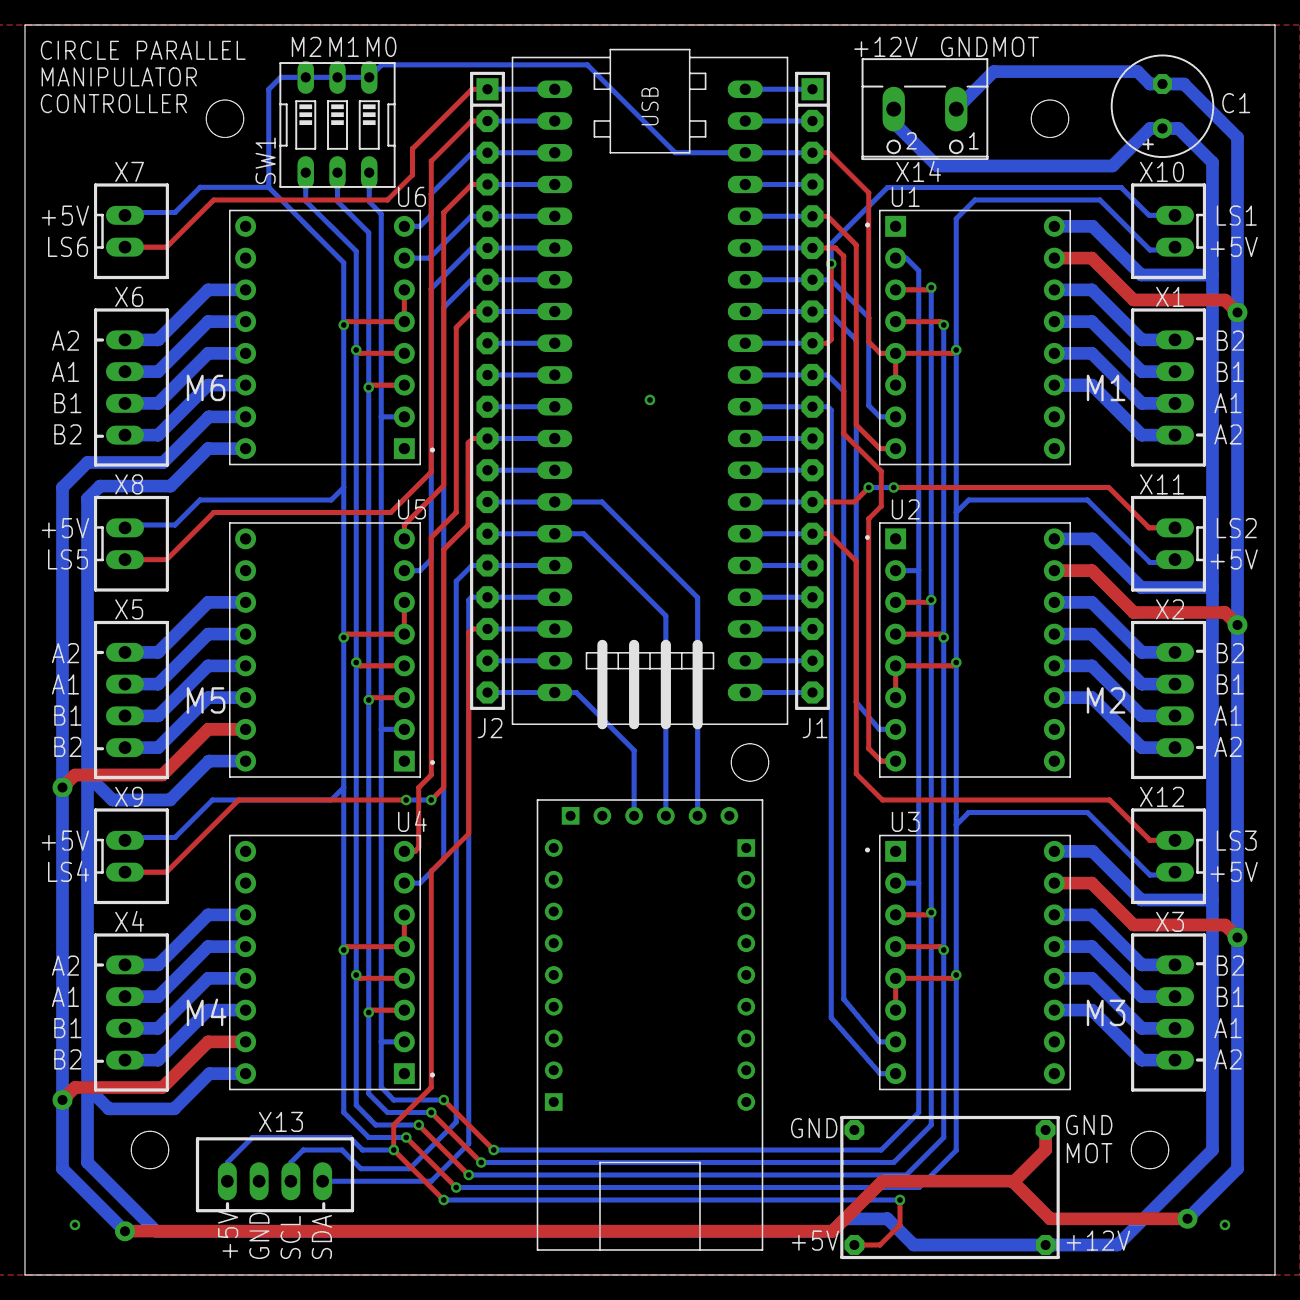
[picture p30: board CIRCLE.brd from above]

Board: 2 copper layers, 100.0 x 100.0 mm, 27 parts (0 on the bottom side), 67 nets.

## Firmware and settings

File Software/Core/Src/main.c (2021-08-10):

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
/* Includes ------------------------------------------------------------------*/
#include "main.h"
#include "adc.h"
#include "i2c.h"
#include "tim.h"
#include "usart.h"
#include "gpio.h"

/* USER CODE BEGIN Includes */
#include "mpu9250.h"
#include "steppermotorcontrol.h"

/* USER CODE END Includes */


void SystemClock_Config(void);
/**
  * @brief  The application entry point.
  * @retval int
  */
int main(void)
{
  /* USER CODE BEGIN 1 */

/*Test*/
char MPUStatus1[] = "MPU 9250 Connected\n";
char MPUStatus2[] = "MPU 9250 Not Connected\n";
char MPUStatus3[] = "MPU 9250 Error\n";


  /* USER CODE END 1 */

  /* MCU Configuration--------------------------------------------------------*/

  /* Reset of all peripherals, Initializes the Flash interface and the Systick. */
  HAL_Init();

  /* Configure the system clock */
  SystemClock_Config();

  /* Initialize all configured peripherals */
  MX_GPIO_Init();
  MX_I2C1_Init();
  MX_TIM3_Init();
  MX_TIM1_Init();
  MX_USART1_UART_Init();
  MX_ADC1_Init();
  /* USER CODE BEGIN 2 */

  /*Start Motor Timers*/
  HAL_TIM_PWM_Start(&htim3, TIM_CHANNEL_4);		/* Start timer of motor 1*/
  HAL_TIM_PWM_Start(&htim3, TIM_CHANNEL_3);		/* Start timer of motor 2*/
  HAL_TIM_PWM_Start(&htim3, TIM_CHANNEL_1);		/* Start timer of motor 3*/
  HAL_TIM_PWM_Start(&htim1, TIM_CHANNEL_3);		/* Start timer of motor 4*/
  HAL_TIM_PWM_Start(&htim1, TIM_CHANNEL_1);		/* Start timer of motor 6*/
  HAL_TIM_PWM_Start(&htim1, TIM_CHANNEL_2);		/* Start timer of motor 5*/


  /*Initialize Inertial Measurement Unit*/
  MPU9250Init();
  AK8963Init();
  /* USER CODE END 2 */

  /* Infinite loop */
  /* USER CODE BEGIN WHILE */
  while (1)
  {
    /* USER CODE END WHILE */

    /* USER CODE BEGIN 3 */

	  bool MPU9250Status = MPU9250IsConnected();

	  if (MPU9250Status == true)
	  {
		  HAL_UART_Transmit(&huart1, (uint8_t *)MPUStatus1, sizeof(MPUStatus1),100);
	  }

	  else if (MPU9250Status == false)
	  {
		  HAL_UART_Transmit(&huart1, (uint8_t *)MPUStatus2, sizeof(MPUStatus2),100);
	  }

	  else
	  {
		  HAL_UART_Transmit(&huart1, (uint8_t *)MPUStatus3, sizeof(MPUStatus3),100);
	  }




	  HAL_Delay(100);
  }
  /* USER CODE END 3 */
}

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
/* USER CODE BEGIN 4 */
void HAL_UART_RxCpltCallback(UART_HandleTypeDef *huart)
{
	__NOP();
}


void HAL_GPIO_EXTI_Callback(uint16_t GPIO_Pin)			/*Callback Function for all the external interrupt functions for limit switches 1-6*/
{
	switch(GPIO_Pin)
	{
	case GPIO_PIN_7 : LimitSwitchStateDetect(1);		/* Limit Switch 1 State Update*/
					  break;

	case GPIO_PIN_2	: LimitSwitchStateDetect(2)	;		/* Limit Switch 2 State Update */
					  break;

	case GPIO_PIN_1	: LimitSwitchStateDetect(3)	;		/* Limit Switch 3 State Update */
					  break;

	case GPIO_PIN_4 : LimitSwitchStateDetect(4)	;		/* Limit Switch 4 State Update */
					  break;

	case GPIO_PIN_12: LimitSwitchStateDetect(5)	;		/* Limit Switch 5 State Update */
					  break;

	case GPIO_PIN_13: LimitSwitchStateDetect(6)	;		/* Limit Switch 6 State Update */
					  break;

	default: 		  break;

	}
}
/* USER CODE END 4 */
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


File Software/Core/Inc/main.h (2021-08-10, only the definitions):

#define INPUT_VOLTAGE_FEEDBACK_Pin GPIO_PIN_0
#define INPUT_VOLTAGE_FEEDBACK_GPIO_Port GPIOA
#define LIMIT_SWITCH_3_Pin GPIO_PIN_1
#define LIMIT_SWITCH_3_GPIO_Port GPIOA
#define LIMIT_SWITCH_3_EXTI_IRQn EXTI1_IRQn
#define LIMIT_SWITCH_2_Pin GPIO_PIN_2
#define LIMIT_SWITCH_2_GPIO_Port GPIOA
#define LIMIT_SWITCH_2_EXTI_IRQn EXTI2_IRQn
#define MOTOR_3_DIR_Pin GPIO_PIN_5
#define MOTOR_3_DIR_GPIO_Port GPIOA
#define MOTOR_3_STEP_Pin GPIO_PIN_6
#define MOTOR_3_STEP_GPIO_Port GPIOA
#define LIMIT_SWITCH_1_Pin GPIO_PIN_7
#define LIMIT_SWITCH_1_GPIO_Port GPIOA
#define LIMIT_SWITCH_1_EXTI_IRQn EXTI9_5_IRQn
#define MOTOR_2_STEP_Pin GPIO_PIN_0
#define MOTOR_2_STEP_GPIO_Port GPIOB
#define MOTOR_1_STEP_Pin GPIO_PIN_1
#define MOTOR_1_STEP_GPIO_Port GPIOB
#define MOTOR_2_DIR_Pin GPIO_PIN_10
#define MOTOR_2_DIR_GPIO_Port GPIOB
#define MOTOR_1_DIR_Pin GPIO_PIN_11
#define MOTOR_1_DIR_GPIO_Port GPIOB
#define LIMIT_SWITCH_6_Pin GPIO_PIN_12
#define LIMIT_SWITCH_6_GPIO_Port GPIOB
#define LIMIT_SWITCH_6_EXTI_IRQn EXTI15_10_IRQn
#define LIMIT_SWITCH_5_Pin GPIO_PIN_13
#define LIMIT_SWITCH_5_GPIO_Port GPIOB
#define LIMIT_SWITCH_5_EXTI_IRQn EXTI15_10_IRQn
#define MOTOR_6_DIR_Pin GPIO_PIN_14
#define MOTOR_6_DIR_GPIO_Port GPIOB
#define MOTOR_5_DIR_Pin GPIO_PIN_15
#define MOTOR_5_DIR_GPIO_Port GPIOB
#define MOTOR_6_STEP_Pin GPIO_PIN_8
#define MOTOR_6_STEP_GPIO_Port GPIOA
#define MOTOR_5_STEP_Pin GPIO_PIN_9
#define MOTOR_5_STEP_GPIO_Port GPIOA
#define MOTOR_4_STEP_Pin GPIO_PIN_10
#define MOTOR_4_STEP_GPIO_Port GPIOA
#define MOTOR_4_DIR_Pin GPIO_PIN_11
#define MOTOR_4_DIR_GPIO_Port GPIOA
#define LIMIT_SWITCH_4_Pin GPIO_PIN_4
#define LIMIT_SWITCH_4_GPIO_Port GPIOB
#define LIMIT_SWITCH_4_EXTI_IRQn EXTI4_IRQn
#define MPU_9250_I2C_SCL_Pin GPIO_PIN_8
#define MPU_9250_I2C_SCL_GPIO_Port GPIOB
#define MPU_9250_I2C_SDA_Pin GPIO_PIN_9
#define MPU_9250_I2C_SDA_GPIO_Port GPIOB

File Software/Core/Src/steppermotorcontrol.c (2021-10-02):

/*
 * Filename			 : steppermotor.c
 * Version No		 : 1.0
 * Version Date		 : 20-03-2021
 * Description		 :
 * External Functions:
 * Internal Functions:
 * Notes			 :


 * Revision History
 * Version No.		 Date			Author 					Email				Description
 * 	  1.0		  20-03-2021	Ayushman Choudhuri	 ayushc205@gmail.com
 *
*/
#include "steppermotorcontrol.h"

/*.........................................Global Variable Definitions.......................................*/

float32_t MotorTargetAngle[6] = {0,0,0,0,0,0};											/*Target angles of respective motors*/
float32_t MotorTargetAnglePrevious[6] = {0,0,0,0,0,0};									/*Previous target angles of respective motors*/
uint8_t   MotorTagetAngleSet[6] = {FALSE,FALSE,FALSE,FALSE,FALSE,FALSE};				/*If target angle has been set (HIGH) or not (LOW)*/
float32_t MotorCurrentAngle[6] = {0.0,0.0,0.0,0.0,0.0,0.0};											/*The current angle of the Motor*/
uint32_t  MotorTargetStepCount[6] = {0,0,0,0,0,0};										/*The total number of steps needed by motors to reach target angle*/
uint32_t  MotorCurrentStepCount[6] = {0,0,0,0,0,0};										/*The total number of steps already excecuted*/
int8_t    MotorDirection[6] = {ANGLE_HOLD,ANGLE_HOLD,ANGLE_HOLD,ANGLE_HOLD,ANGLE_HOLD,ANGLE_HOLD};	/*The direction in which the motor needs to move*/
uint8_t   MotorState[6] = {HIGH,HIGH,HIGH,HIGH,HIGH,HIGH};								/*Motor Running - HIGH , Motor Stop - LOW*/
uint8_t   MotorHighStateSetFlag[6] ={LOW, LOW, LOW, LOW, LOW, LOW};								/*If the motor state has already been set once*/

uint8_t	  LimitSwitchState[6] = {LOW, LOW, LOW, LOW, LOW, LOW};
uint8_t   LimitSwitchMode[6] = {LOW, LOW, LOW, LOW, LOW, LOW};
uint32_t  LimitSwitchCounter[6] = {0,0,0,0,0,0};


int8_t test = 0;
uint32_t test2 = 0;
uint8_t test3 = 0;
uint32_t TestCounter  = 0;
uint32_t TestSetIndex = 0;
/*........................................Function Definitions...............................................*/

/*
 * Function Name	 			: LimitSwitchDebounce
 * Function Description 		: Function performs debouncing operation on the incoming limit switch signal stored in LimitSwitchState[].
 * 								  If a limit switch signal passes the debounce test, the LimitSwitchMode[] for the limit switch is set to HIGH.
 *
 * Return Type					: void
 * Return Type Description 		: N/A
 *
 * Parameter(s)					: limit_switch_index
 * Parameter Description		: limit_switch_index : The index of the limit switch for a specific motor. The values vary from 1 for the limit switch of Motor 1
 * 													   to 6 for the limit switch of the 6th motor.
 * Global Variables Accessed	: LimitSwitchCounter[], LimitSwitchMode
 * Global Variable(s) Modified	: LimitSwitchCounter[],
 * Library Function(s) Called	: N/A
 * Called by					: LimitSwitchTriggerScan()
 *  Notes			 			: Tune the LIMIT_SWITCH_DEBOUNCE_THRESHOLD configuration parameter to increase or decrease the debounce threshold.

 * Change Log
 * Version No.		 Date			Author 					Email				Description
 * 	  1.0		  20-03-2021	Ayushman Choudhuri	 ayushc205@gmail.com		base file
*/

static void LimitSwitchDebounce(uint32_t limit_switch_index)
{
	switch(LimitSwitchState[limit_switch_index -1])
	{
		case LOW:	LimitSwitchCounter[limit_switch_index - 1] = 0;
					LimitSwitchMode[limit_switch_index - 1] = LOW;
					break;

		case HIGH:	LimitSwitchCounter[limit_switch_index -1] ++;

					if (LIMIT_SWITCH_DEBOUNCE_THRESHOLD <= LimitSwitchCounter[limit_switch_index -1])
					{
						LimitSwitchMode[limit_switch_index -1] = HIGH;
					}

					else
					{
						LimitSwitchMode[limit_switch_index -1] = LOW;

					}

					break;

		default: 	break;
	}
}

/*
 * Function Name	 			: LimitSwitchStateDetect
 * Function Description 		: This function determines the state of the limit switch
 * 								  HIGH : Switch is triggered (Closed position)
 * 								  LOW : Switch is not triggered (Open Position)
 * Return Type					: void
 * Return Type Description 		: None
 *
 * Parameter(s)					: limit_switch_index
 * Parameter Description		: limit_switch_index : The index of the limit switch for a specific motor. The values vary from 1 for the limit switch of Motor 1
 * 													   to 6 for the limit switch of the 6th motor.
 * Global Variables Accessed	: LimitSwitchState[]
 * Global Variable(s) Modified	: LimitSwitchState[]
 * Library Function(s) Called	:
 * Called by					: HAL_GPIO_EXTI_Callback()
 *  Notes			 			: To use this function for the limit switch, please set the interrupt trigger to both rising and falling edges

 * Change Log
 * Version No.		 Date			Author 					Email				Description
 * 	  1.0		  20-03-2021	Ayushman Choudhuri	 ayushc205@gmail.com
*/

void LimitSwitchStateDetect(uint32_t limit_switch_index)
{
	switch (LimitSwitchState[limit_switch_index -1]) /*Every time the function is triggered from the external interrupt, the updated value is the opposite of the old value*/
								  {
						  	  	  case LOW:  LimitSwitchState[limit_switch_index -1] = HIGH;
						  	  	  	  	  	 break;

						  	  	  case HIGH: LimitSwitchState[limit_switch_index -1] = LOW;
						  	  	  	  	  	 break;

						  	  	  default: break;
								  }
}

/*
 * Function Name	 			: LimitSwitchTriggerScan
 * Function Description 		: Function scans all the limit switches and updates the state variables to detect the switch mode.
 * Return Type					: void
 * Return Type Description 		: N/A
 *
 * Parameter(s)					: None
 * Parameter Description		: None
 * Global Variables Accessed	: None
 * Global Variable(s) Modified	: None
 * Library Function(s) Called	:
 * Called by					: SysTick_Handler()
 *  Notes			 			:

 * Change Log
 * Version No.		 Date			Author 					Email				Description
 * 	  1.0		  20-03-2021	Ayushman Choudhuri	 ayushc205@gmail.com
*/

void LimitSwitchTriggerScan(void)
{
	for(uint8_t switch_index = 1; switch_index <=6 ; switch_index ++)
	{
		LimitSwitchDebounce(switch_index);
	}
}

/*
 * Function Name	 			: MotorStopTriggerDetect
 * Function Description 		:
 * Return Type					:
 * Return Type Description 		:
 *
 * Parameter(s)					: None
 * Parameter Description		: None
 * Global Variables Accessed	: None
 * Global Variable(s) Modified	: None
 * Library Function(s) Called	:
 * Called by					:
 *  Notes			 			:

 * Change Log
 * Version No.		 Date			Author 					Email				Description
 * 	  1.0		  20-03-2021	Ayushman Choudhuri	 ayushc205@gmail.com
*/

static void MotorStopTriggerDetect(uint8_t motor_index)
{
	switch(LimitSwitchState[motor_index -1])
	{
		case HIGH: MotorState[motor_index -1] = LOW;
				   MotorCurrentAngle[motor_index - 1] = 0;
				   break;
		case LOW:  MotorState[motor_index - 1] = HIGH;
				   MotorHighStateSetFlag[motor_index] = LOW;
				   break;

		default:   break;
	}

}
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

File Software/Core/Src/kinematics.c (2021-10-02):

/*
 * Filename			 : kinematics.c
 * Version No		 : 1.0
 * Version Date		 : 20-01-2021
 * Description		 : This source file contains all the static and external functions needed to solve the inverse kinematics of a 6DOF RSS Parallel Manipulator
 * External Functions:
 * Internal Functions:
 * Notes			 :


 * Revision History
 * Version No.		 Date			Author 					Email				Description
 * 	  1.0		  20-01-2021	Ayushman Choudhuri	 ayushc205@gmail.com
 *
*/

#include "kinematics.h"
#include "steppermotorcontrol.h"
/*.........................................Global Variable Definitions.......................................*/
float32_t EndEffectorCoordinates[6][3] = 				{{ 73.7, 19.46, 0},
														 { 53.7 ,54.1 , 0},
													 	 { -53.7  ,54.1 ,0},
													 	 {-73.7, 19.46, 0},
													 	 {-20 ,-73.55 ,0},
													 	 { 20, -73.55 , 0}};	/*Coordinates (in mm) of the end effector pivot point coordinates with respect to the end effector frame of reference.*/

uint32_t EndEffectorCoordinatesSize[2] = {6,3};

float32_t BaseCoordinates[6][3] = 					 {{ 81.63, 0.36, 0},
		 	 	 	 	 	 	 	 	 	 	 	  { 41.13 , 70.51, 0},
													  {-41.13, 70.51 ,0},
													  {-81.63, 0.36, 0},
													  { -41.13 ,-70.51 ,0},
													  {41.13, -70.5, 0}};	/*Coordinates (in mm) of the base pivot point coordinates with respect to the base frame of reference. */

uint32_t BaseCoordinatesSize[2] = {6,3};

const float32_t MotorPlaneAngle[6] = 					 {-pi/3 , 2*pi/3 , - 2*pi/3 , pi/3 , -pi , 0 };




float32_t MotorAngles[6] = {0,0,0,0,0,0};										/*Variable stores the motor angles of all the 6 motors in order from 1 to 6*/


float32_t PoseSetpoint[6] = {0,0,0,0,0,0};										/*Instance of the Pose structure used to store the Pose Setpoint*/

float32_t RotationMatrix[3][3] = {{0,0,0},{0,0,0},{0,0,0}};						/*Variable stores the rotation matrix to express end effector coordinates with respect to base frame*/
uint32_t  RotationMatrixSize[2] = {3,3};

float32_t TranslationVector[3][1] = {{0},{0},{0}};								/*Variable Stores the Translation Vector between the base frame and the end effector frame*/
uint32_t  TranslationVectorSize[2] = {3,1};

float32_t EffectiveLinkLengthMatrix[6] = {0,0,0,0,0,0};							/*Variable stores the effective link lengths of the RSS link structures*/
uint32_t  EffectiveLinkLengthMatrixLength = 6;

float32_t EndEffectorCordTransform[3][6] = {{0,0,0,0,0,0},
											{0,0,0,0,0,0},
											{0,0,0,0,0,0}};


//uint32_t  EndEffectorCordTransformSize = {3,6};

/*........................................Function Definitions...............................................*/

/*
 * Function Name	 			: RotationMatrixUpdate
 * Function Description 		: Calculates the Rotation matrix to transform coordinates from end effector frame to base frame
 * 								  The function takes inputs from the global structure PoseSetpoint which stores the current pose setpoint for the end effector
 * Return Type					: None
 * Return Type Description 		: None
 * Parameter(s)					: None
 * Parameter Description		: None
 * Global Variables Accessed	: PoseSetpoint.Yaw, PoseSetpoint.Pitch, PoseSetpoint.Roll
 * Global Variable(s) Modified	: RotationMatrix
 * Library Function(s) Called	: None
 * Called by					:
 *  Notes			 			: All the angle setpoints need to be in degrees and shall be converted into radians in the function before being used in the rotation matrix

*/

static void RotationMatrixUpdate()
{
	/*Declare Local Variables*/
	float32_t Y = 0.0174*PoseSetpoint[0]; /*Convert Yaw Setpoint from degrees to radians*/
	float32_t P = 0.0174*PoseSetpoint[1];/*Convert Pitch Setpoint from degrees to radians*/
	float32_t R = 0.0174*PoseSetpoint[2];/*Convert Roll Setpoint from degrees to radians*/

	RotationMatrix[0][0] = cos(Y)*cos(P);
	RotationMatrix[0][1] = -(sin(Y)*cos(R)) + (cos(Y)*sin(P)*sin(R));
	RotationMatrix[0][2] = (sin(Y)*sin(R)) + (cos(Y)*sin(P)*cos(R));
	RotationMatrix[1][0] = sin(Y)*cos(P);
	RotationMatrix[1][1] = (cos(Y)*cos(R)) + (sin(Y)*sin(P)*sin(R));
	RotationMatrix[1][2] = -(cos(Y)*sin(R)) + (sin(Y)*sin(P)*cos(R));
	RotationMatrix[2][0] = -sin(P);
	RotationMatrix[2][1] = cos(P)*sin(R);
	RotationMatrix[2][2] = cos(P)*cos(R);
}

/*
 * Function Name	 			: TranslationVectorUpdate
 * Function Description 		: Calculates the position vector of the end effector frame origin with respect to the base frame
 * Return Type					: None
 * Return Type Description 		: None
 * Parameter(s)					: None
 * Parameter Description		: None
 * Global Variables Accessed	: PoseSetpoint.delx, PoseSetpoint.dely, PoseSetpoint.delz
 * Global Variable(s) Modified	: TranslationVector
 * Library Function(s) Called	: None
 * Called by					: all the units are in mm
 *  Notes			 			:
*/

static void TranslationVectorUpdate()
{
	TranslationVector[0][0] =  PoseSetpoint[3];
	TranslationVector[1][0] =  PoseSetpoint[4];
	TranslationVector[2][0] =  PoseSetpoint[5] + HOME_POSITION_Z_OFFSET;
}

/*
 * Function Name	 			: EffectiveLinkLengthCalculationVectorized()
 * Function Description 		: Calculation of effective link length between Bi and Ei using a vectorized approach
 * Return Type					: void
 * Return Type Description 		: None
 * Parameter(s)					: None
 * Parameter Description		: None
 * Global Variables Accessed	: EndEffectorCoordinates,BaseCoordinates,RotationMatrix,RotationMatrixSize,TranslationVector,TranslationVectorSize
 * Global Variable(s) Modified	: EndEffectorCoordinates,BaseCoordinates,RotationMatrix,TranslationVector
 * Library Function(s) Called	: MatrixMultiply,MatrixSubtract,MatrixAdd,sqrt
 * Called by					:
 *  Notes			 			:
*/
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

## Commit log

2021-05-29 New motor system initialization branch added
2021-05-29 TIM3 CH1 initialized to PWM Generation mode on a 10 KHz Frequency
2021-06-06 Motor Timers Initialized and Step Angle Testing for Motor 1
2021-07-21 Stable Limit Switch Detection Logic
2021-07-21 Updated Limit Switch Detection Logic
2021-07-22 Updated Motor Angle Function
2021-08-01 Updated MotorAngle Function
2021-08-03 Corrected Motor Actuation Function and updated hardware level motor control routine in Systick Loop.
    [main.c, steppermotorcontrol.c, steppermotorcontrol.h]
2021-08-08 Updated Motor Angle Test function and resolved Motor 5 direction issue ( Motor 5 direction pin was set to PA15 and has now been changed to PB15 as per controller hardware circuit)
    [Circle_Software.ioc, main.h, steppermotorcontrol.c]
2021-08-08 Temporary fix to the issue of MotorCurrentStepCount variable of data type uint32_t overshooting below 0 when the angle is decreasing. A more elegant solution will be implemented later
    [steppermotorcontrol.c]
2021-10-02 1. Robot CAD model added 2. Controller PCB files added
    [100x100 new PCB model.SLDPRT, 12cm x 18cm PCB Board.SLDPRT, 40x40x10 DC Fan.SLDPRT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]
2021-11-28 Inverse Kinematics Solver Updated

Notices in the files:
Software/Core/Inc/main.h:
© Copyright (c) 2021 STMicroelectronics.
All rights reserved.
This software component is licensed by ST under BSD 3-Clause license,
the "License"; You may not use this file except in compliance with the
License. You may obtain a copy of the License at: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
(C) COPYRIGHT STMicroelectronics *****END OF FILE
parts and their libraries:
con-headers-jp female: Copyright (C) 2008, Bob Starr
